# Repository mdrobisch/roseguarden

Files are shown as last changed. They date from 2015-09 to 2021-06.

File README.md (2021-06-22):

RoseGuarden
===========

A remote door api and web application for Raspberry Pi, Odroid, Orange Pi or BeagleBoard (based on python).

Important news
==============

**Because of issues in the very base of the system design, we decided to make a compelete rework of roseguarden**
**Ther will be no bugfixes or features in this version of roseguarden**

Features
========

* affordable access-control system
* authentication by rfid-tags or webserver-application (smarthone, tablet)
* easily extendable for additional doors. through network based system
* 3 different user-roles (user, supervisor, admin) for managing accesses and viewing logs
* different types of accesses (period, days-budget)
* additional options to adjust accesses (by given time, weekdays, differenet door-licences)
* basic statistics (total users, total accesses, accesses per weekday, accesses per door/node)

Roadmap
=======

Roseguarden is in development. Till now there exist only a prerelease version. It's already working fine and can be installed/ setup using the instruction below. So far it is not a released version. The following steps are planed till release and further. While there is only one contributor to the project by now, don't expect a release soon. It's done when it's done. Find news about the progress in the community-forum.

* ~~Build up and run a community forum~~ [Finished 2017-01-17 [Community forum](http://www.community.fabba.space/)].
* ~~Integrate the http-server into flask~~ [Finished 2017-02-19].
* Implement a web-gui setup to make setup easier. [In development]
* Package Roseguarden into images (ISO) for Raspberry Pi 2, 3 and Zero. [planned]
* Provide a user manual for important task and usage of Roseguarden [planned]
* __**Release version 1.0.0 images**__ [planned]
* Integrate a tool to repair broken rfid-tags [planned]
* Build a web-gui export and import feature for user-backup [planned]
* Build in user groups for easy handling of multiple users [planned]
* __**Release Version 1.1.0**__ [planned]

Backlog for further release:
---------------------------

* OLED display support
* Replace SPI-Py package with a more stable module
* Rework RFID-module
* support for machine-control (enable/license machines)
* support a cashless payment system

News & Community
================

**Want to see Roseguarden in action: Visit Roseguarden on the Maker-Faire-Saxony in Chemnitz Germany (22./23. April 2017)**

The project has a community forum. News will be posted there. In addition its purpose is to find help, discuss features or report bugs. You are welcome to contribute to the project there.

[To the community forum](http://www.community.fabba.space/)

Overview
========

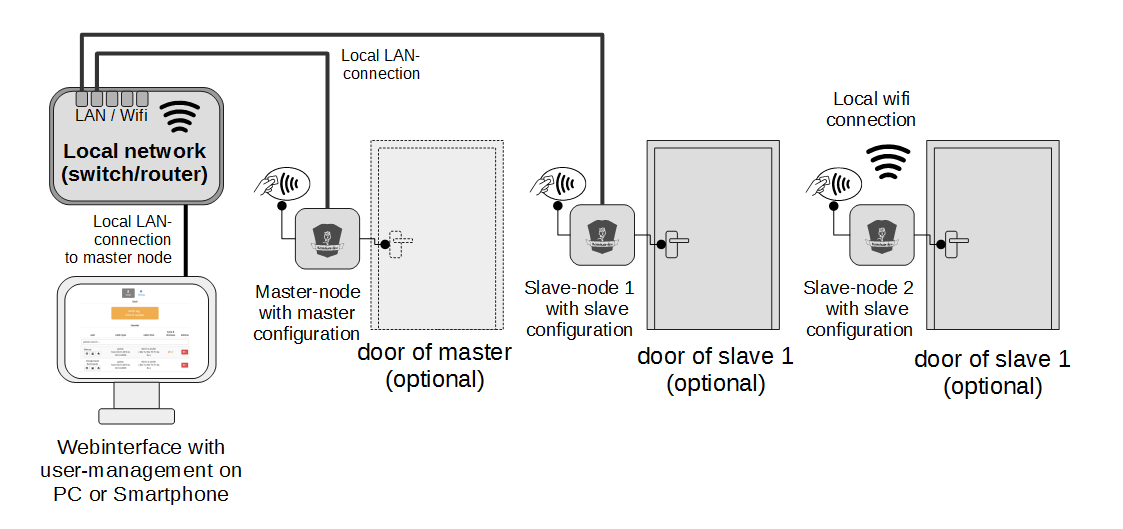
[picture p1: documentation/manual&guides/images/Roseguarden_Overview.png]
overview


Quickstart
==========

Update your system
------------------

First of all update and upgrade your raspberry pi os

1. `sudo apt-get update`
2. `sudo apt-get upgrade`

Install basic dependecies
-------------------------

3. `sudo apt-get install git`

Install RoseGuarden
-------------------

Clone the repository to your installation path with `git clone https://github.com/blinzelaffe/roseguarden.git`

Install dependencies
--------------------

For the frontend we need nodejs to get a module called bower and a fast nodejs http-server.
The http-server serve the http-request. Bower will handle all the frontend dependencies.
You can install the most actual nodejs package like this.

4. `wget http://node-arm.herokuapp.com/node_0.10.36_armhf.deb`
5. `sudo dpkg -i node_0.10.36_armhf.deb`

NOTE: for the old raspberry pi the nodejs 0.10.36 is used. Some newer versions have problems with the c++ libaries.
Have a look at http://weworkweplay.com/play/raspberry-pi-nodejs/ for further informations and instructions.
The newest nodejs-version 4.2.1 suppose to have direct raspberry pi (ARM6/ARM7) support included.
It has to be tested with RoseGuarden.

Alternative way to install LTS version of nodejs (4.2.4) for raspberry pi

for raspberry pi A,B,B+ :
wget https://nodejs.org/dist/v4.2.4/node-v4.2.4-linux-armv6l.tar.xz
tar -xvf node-v4.2.4-linux-armv6l.tar.xz
cd node-v4.2.4-linux-armv6l
sudo cp -R {bin,include,lib,share} /usr/local/

or for raspberry pi 2:
wget https://nodejs.org/dist/v4.2.4/node-v4.2.4-linux-armv7l.tar.xz
tar -xvf node-v4.2.4-linux-armv7l.tar.xz
cd node-v4.2.4-linux-armv7l
sudo cp -R {bin,include,lib,share} /usr/local/

First we install the nodejs-http-server
For this step you have to switch to the `client`-directory and prompt

6. `sudo npm install -g http-server`

Now we could install bower and let bower get us the packages for the frontend (css, angularjs, smarttable, etc.).
In the same `client`-directory prompt

7. `sudo npm install -g bower`
8. install the bower packages with `bower install` (in the `client`-directory install)

Now the frontend is ready.

For the backend (python) we have to install dependecies, too.

First we install `python-dev` and `gcc` on the raspberry to establish interfaces between c++-libs and python.

9. `sudo apt-get install python-dev` needed to compile c++-bindings with python
10. `sudo apt-get install gcc libjpeg-dev zlib1g-dev` needed to compile c++, jpge and zlib

The python package manager `pip` will handle needed python modules for us. So we need to install `pip` like this.

11. `sudo apt-get install python-pip`

At this point we will get the python packages list in the `requirement.txt` file.
Switch to the `server`-directory and prompt.

12. `sudo pip install -r requirements.txt` (in the `server`-directory)

To use the rfid-reader (rc522) we have to install SPI-Py. Switch to the `server/app/SPI-Py`-directory and
install the dependencies and the module.

13. `sudo python setup.py install` install the module

Note: depending on your raspberry pi and kernel you have to re/enable the spi-module and the device tree support
with `sudo raspi-config` -> 'Advanded Options'

Initial steps
-------------

- copy the template `config.template.ini` in the `server` - directory to `config.ini` with `cp config.template.ini config.ini`
- change settings to your requirements
- initialize RoseGuarden database in the `server` - directory with `sudo python roseGuarden.py create_db`

Running RoseGuarden
-------------------

- start the http-server in the `client` - directory with  `http-server -p 8000`
- start the RoseGuarden-app in the `server` - directory with `sudo python roseGuarden.py start`

Use RoseGuarden
----------------

- after complete installation and setup you can reach the admin panel on the ip of your raspberry pi (port 8000)
- e.g. enter "192.168.1.100:8000" in your browser (Chrome or Mozilla are suggested)

- The initial administrator-account is: Administrator
- The initial administrator-password is: pleasechangethepassword
- please change the password after your first login

Problems durring installation and running RoseGuarden
-----------------------------------------------------

** _Problem:_ **

Modules (e.g. Flask) could not found while running `sudo python roseGuarden.py create_db` or `sudo python roseGuarden.py start`

** _Solution:_ **

- Go to `/your-roseguarden-directory/server/`
- repeat the installation of the python modules with `sudo pip install -r requirements.txt`
- sometime there are problems with a bad internet connection, check this twice before running the installation (e.g. ping to a known web-site)

** _Other Hints:_ **

Some other known issues regarding the WLan and the RFID-Reader can be found at the end of the page.

Have a look at the known issues on Github ( https://github.com/blinzelaffe/roseguarden/issues?utf8=%E2%9C%93&q=is%3Aissue+ ) and see problems already known.

Sometimes a update will help to get the latest version of RoseGuarden and some fixed bugs. See the section below for this.

Update RoseGuarden
------------------

For updating RoseGuarden stop its running process.

To update the software to the latest version on github, use git.

- `git fetch --all`
- `git reset --hard origin/master`

Now switch to the `server`-directory:

If some new external pip-modules are introduces in a version you need to reload the `requirements.txt`.

- `sudo pip install -r requirements.txt`

In addition a upgrade of the migration from the database is required, use roseGuarden.py.

- `sudo python roseGuarden.py db upgrade`

For migrations or upgrades of the database, new data have to been seeded (storing default values). So please run,

- `sudo python roseGuarden.py seed`

To update the client switch to your client directory e.g the `client`-directory:

Here we have to install/uninstall all new/old packages of bower.

- `bower install` (no `sudo` required)

After updating please restart your roseGuarden-application again.
It should be work after this with the newest version for server and client.

Install autostart and montoring (supervisor)
============================================

After testing roseGuarden on the system you can add a autostart and monitoring of the application and the http-server.
We use supervisor for this purpose.

You can install supersior from distribution package

- `sudo apt-get install supervisor`

- `sudo service supervisor restart`

The config of supervisord is stored on your system in the following file: `/etc/supervisor/supervisord.conf`.
There is a template in the repository `documentation/templates&scripts/supervisord.config`.
Use the file to adapt it to your system (especially the pathes).

Screenshots (Software)
======================

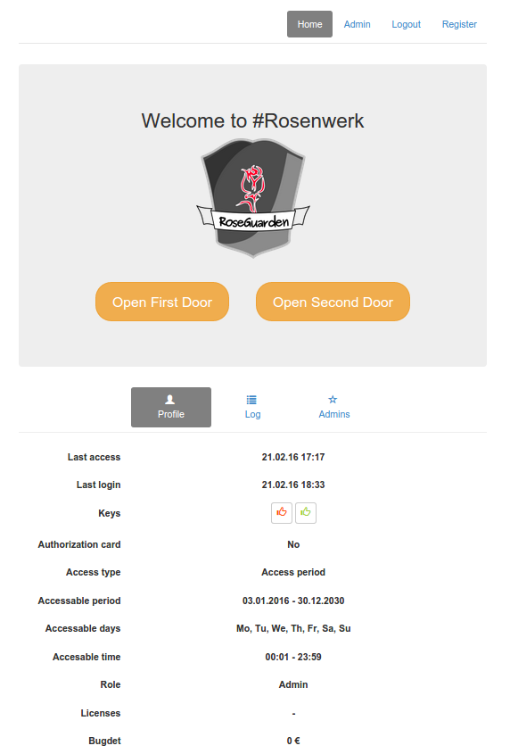
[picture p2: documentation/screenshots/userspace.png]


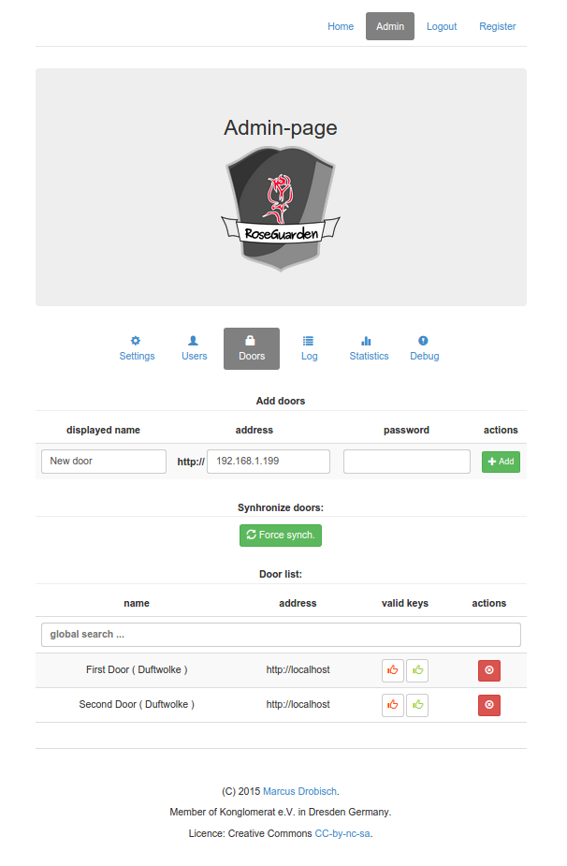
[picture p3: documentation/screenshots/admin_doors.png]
doors


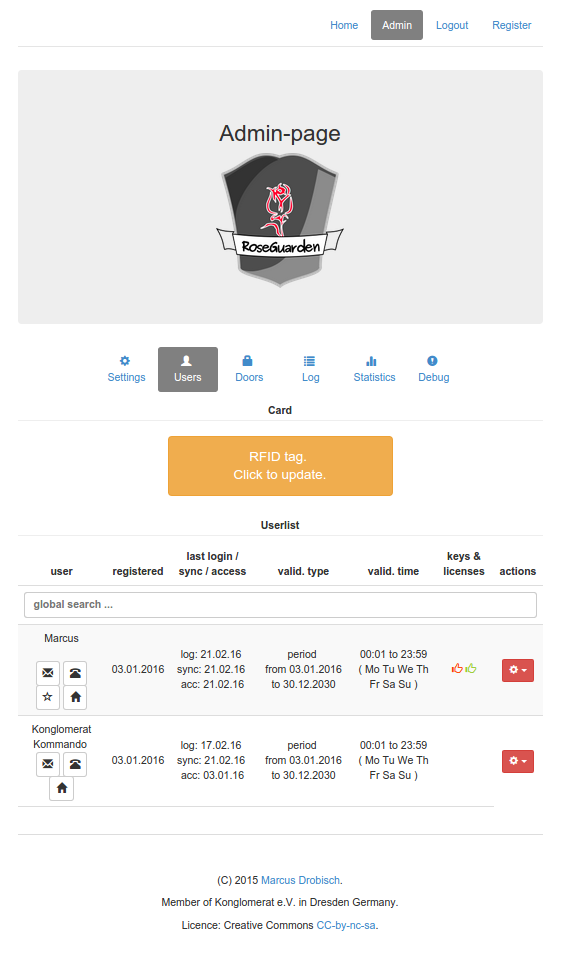
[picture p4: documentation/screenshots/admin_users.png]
users


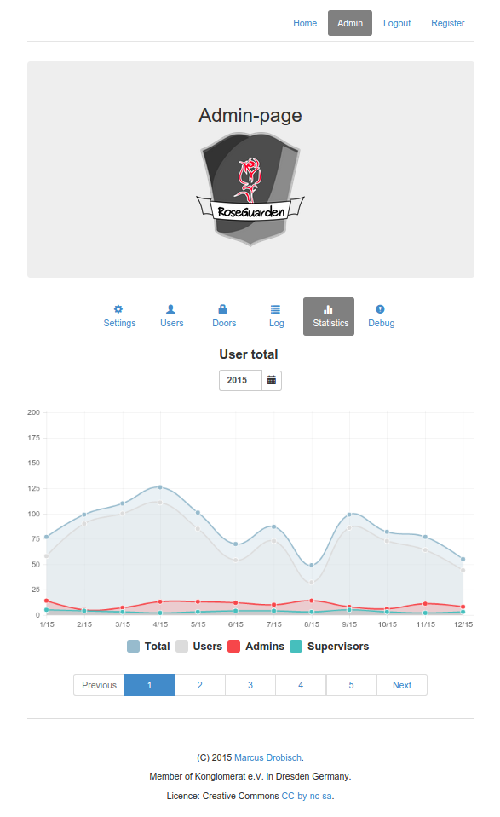
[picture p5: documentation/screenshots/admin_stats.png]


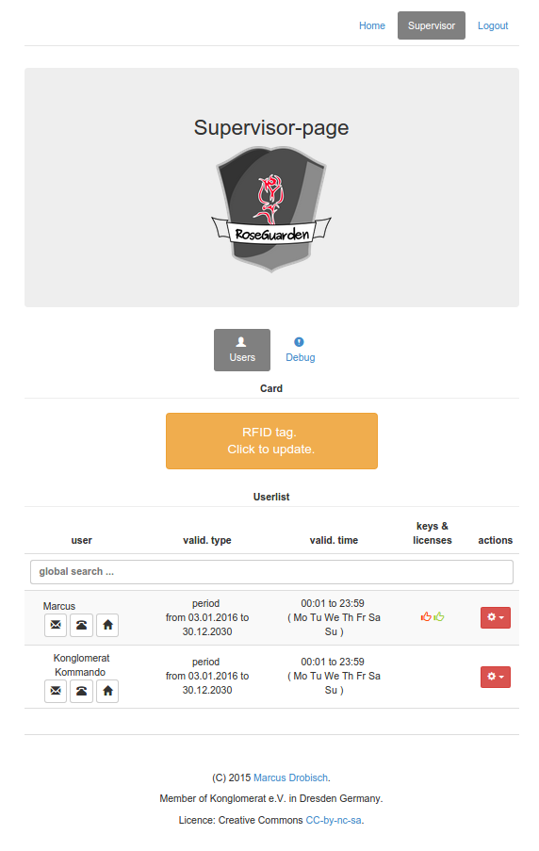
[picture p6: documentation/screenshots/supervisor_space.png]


Hardware
========

The hardware consists of the following electronics  types mounted on a board.

- the control unit (Rapsberry Pi, Orange Pi, Beagleboard or Odroid): running the Python based app and server.
- a RFID-reader (e.g. RC552): reading and writing the tags
- a relay-module: controling the door-openers
- a dc-dc-converter: supplying the control unit with a input  of e.g. 12V / 24V and a output of 5V
- a micro-usb cable of 30cm length: connect dc-dc-converter to the control unit
- some internal cable: e.g. from dc-dc converter to the relay module or to the raspberry pi

Screenshots (Hardware)
----------------------

Here some photos of the assembled and mounted Roseguarden device in the early stage.

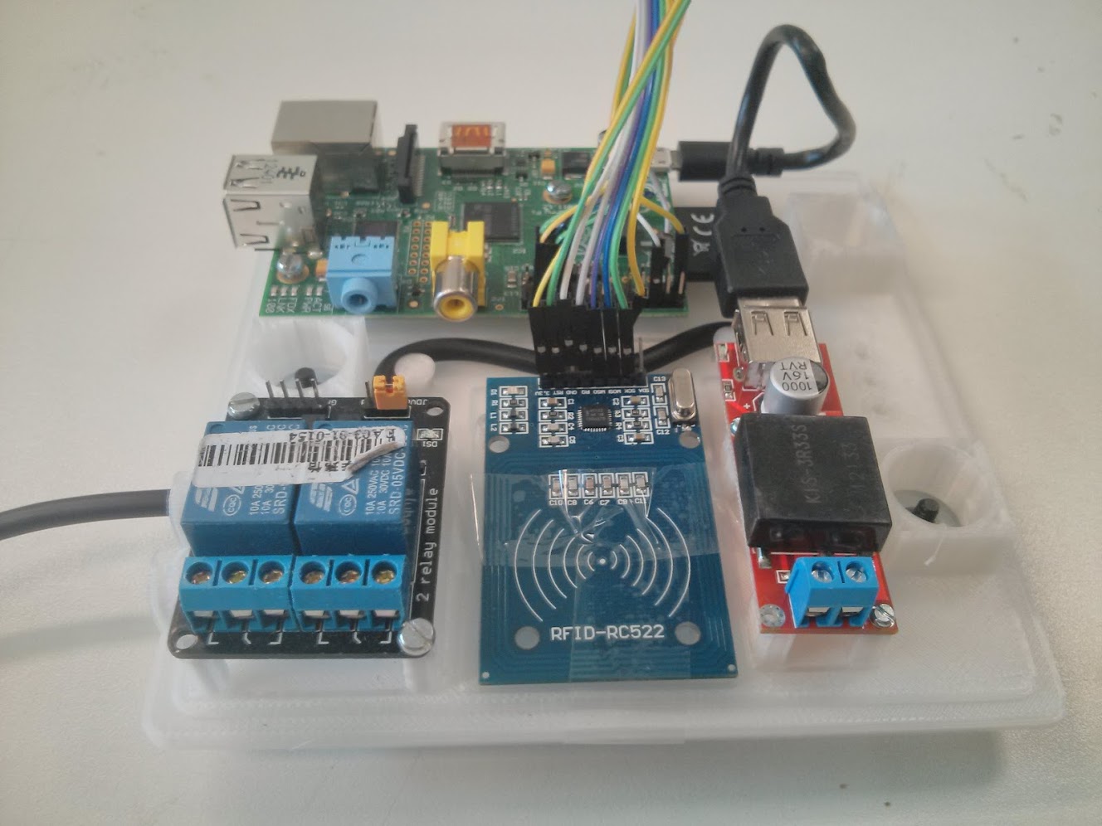
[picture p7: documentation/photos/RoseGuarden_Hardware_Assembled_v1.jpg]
 

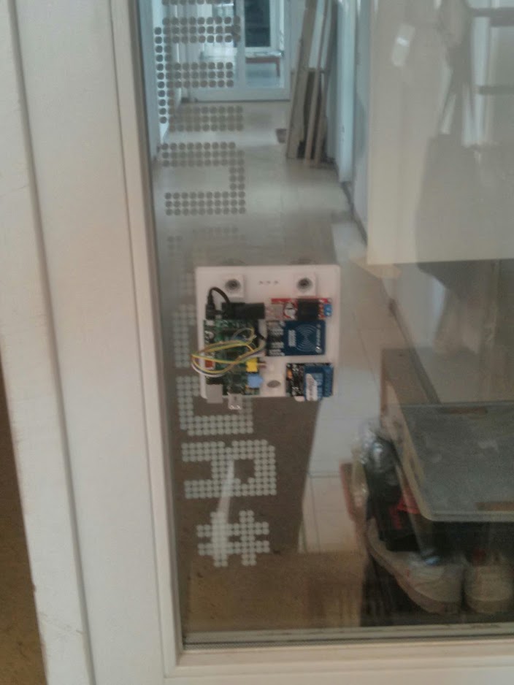
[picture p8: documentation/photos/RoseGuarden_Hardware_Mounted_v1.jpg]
 

Recommended bill of material
----------------------------

We recommend the following tested devices:

- Rapsberry Pi 1 B (found on watterot, rs online, digikey)
- KIS3R33S dc-dc converter (found on ebay from various distributoirs from about 3€ per piece)
- RC552 rfid reader, including 2 rfid-tags (found on ebay from various distributors from about 3€ per piece)
- SainSmart 2 ch. relay module or compatible (found on ebay from various distributors and producers from about 3€ per piece)
- the 3d-printed case on below
- 4 x M2 and 10 x M3 screws to mount the electronic to the case

additional for connecting and supllying the device:

- some breadboard female-female connector (found on pollin, watterot or sparkun)
- some cable with at least 3 wires @ 1A (found on pollin, reichelt, digikey or your local electronic store)
- a ethernet-patch-cable (found on pollin, reichelt, digikey or your laocal electronic store)
- or a wifi-dongle (found on pollin, reichelt, digikey or your laocal electronic store)

additional for mounting the device on walls or doors:

- suckers with 40mm diameter and M4-bolts (found on ebay from various distributors from about 7€ per 10 pieces)
- or glue tape for mounting
- or screws for mounting 

Case and Mounting
-----------------

The case ist modeled with the powerful open source software FreeCAD. Have a look in the hardware folder for the current stable version of the board and its case. It is designed to be 3d-printed with dimensions of 145mm x 145mm x 60mm. The design uses suckers to mount the device to windows or doors. With a few modifications you can also use screws for a more stable mounting. Be aware that the RFID-communication could only reach throw about 30mm non-metallic walls or glass (+ aboout 20mm rfid-module-to-wall distance). 

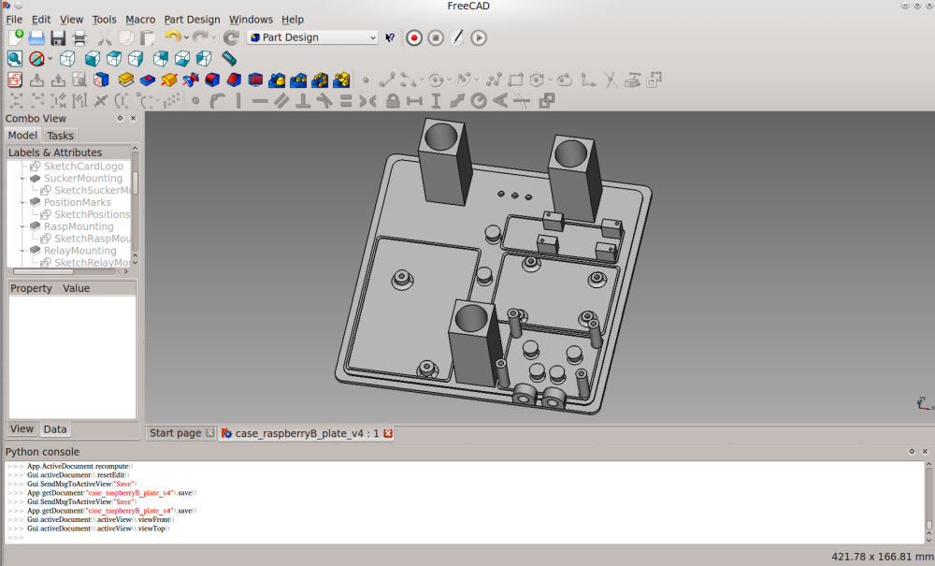
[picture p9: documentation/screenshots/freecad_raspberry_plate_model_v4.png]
freecad
 

Feel free to change the design to your needs. Please share your changed designs and new versions with the community (by asking for a push request). 

Assembly
--------

To assemble the components, you only need some additional M2 and M3 screws to put the electronics on the board. While using other electronics than recommended, change the board modell to your needs. The positions are marked for easy assembly. The cable can put throw cable holes and routed along dedicated bolts.

The schematic show the connection between raspberry pi and the modules.

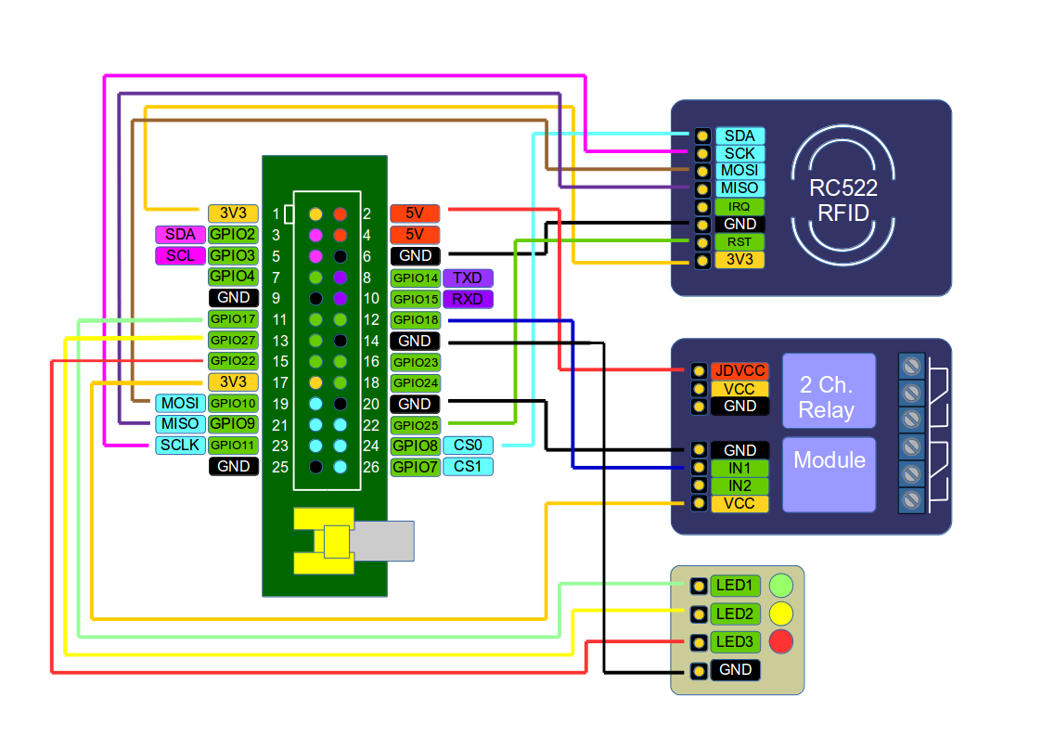
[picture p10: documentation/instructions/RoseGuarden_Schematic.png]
schematic


Further Documentation
=====================

Further documentation and information on components and installation could be found on the project-wiki http://h2371910.stratoserver.net/projects/tuer-und-geraeteverwaltung-rosenguarden/wiki/Wiki (german language only, please translate via google translate or other services).

Troubleshooting
===============

*The WLAN connection breaks ofter some time*

Normally the wlan connection timed out after a while.
The default config of raspberry pi (wheezy) don't reconnect to disappearing networks.
To fix this the following steps could enable the reconnection.

- change to /etc/ifplugd/action.d/ with `cd /etc/ifplugd/action.d/`
- copy the ifupdown file to ifupdown.original (for backup) with: `sudo cp ifupdown ifupdown.original`
- overwrite ifupdown with the alternative ifupdown from the wpa_supplicant-folder with:  `sudo cp /etc/wpa_supplicant/ifupdown.sh ./ifupdown`
- reboot with `sudo reboot`

Alternativly you can tools like wicd-curses.
Instructions for wicd-curses can be found in the internet.

*I have problems to develop under windows*

- Install the python Visual C++-Compiler from  http://aka.ms/vcpython27 before installing the requirements
- user requirements_win_dev.txt instead of requirements.txt (SPI-Py is for linux only)

*The rfid don't read any tag*

With Kernel 3.18 and above Rasbian switch to device tree support on default.
A detailed description is shown here: https://www.raspberrypi.org/forums/viewtopic.php?t=97314
This could encounter problems with the spi.

To fix the issue you have to re/enable the spi-module.
To setup this use `sudo raspi-config` -> 'Advanded Options' or write the changes directly to `/boot/config.txt`
on your own.

For Raspbbery Pi B

`dtparam=spi=on`

`dtoverlay=spi-bcm2708`

have to been set.

For Raspberry Pi 2 (not tested, yet)

`dtparam=spi=on`

`dtoverlay=spi-bcm2835`

should be working (not tested yet)

For Raspberry Pi 2 please consider, there is be a another pin-out-connectio needed. Some instructions described here:
https://www.raspberrypi.org/forums/viewtopic.php?f=37&t=106313 or a alternative way to enable SPI here http://bsd.ee/~hadara/blog/?p=1017

Mifare_RC522_RFID Raspberry Pi 2 B

MOSI ——————————> pin 19 e.g. GPIO 10

MISO ——————————> pin 21 e.g. GPIO 9

SCLK ——————————> pin 23 e.g. GPIO 11

SDA  ——————————> pin 24 e.g. GPIO 8

RST  ——————————> pin 22 e.g. GPIO 25

IRQ  ——————————> NONE

In addition you have to change your SPI-Py library. There is a bug, which isn't fixed and break the communication to the Mifare-Module.

change the following code in the `/server/app/SPI-Py/spi.c`-file.

```c
	struct spi_ioc_transfer tr = {
		.tx_buf = (unsigned long)tx,
		.rx_buf = (unsigned long)rx,
		.len = tupleSize,
		.delay_usecs = delay,
		.speed_hz = speed,
		.bits_per_word = bits,
        .cs_change = 1,
    };
```

to

```c
	struct spi_ioc_transfer tr = {
		.tx_buf = (unsigned long)tx,
		.rx_buf = (unsigned long)rx,
		.len = tupleSize,
		.delay_usecs = delay,
		.speed_hz = speed,
		.bits_per_word = bits,
        .cs_change = 0,
	};
```

License
=======

RoseGuarden is published under the terms of the GPL v3 license. See [LICENSE](LICENSE).

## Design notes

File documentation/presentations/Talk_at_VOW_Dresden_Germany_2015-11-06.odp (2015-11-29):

## DIE FLEXIBLE WERKSTATT ZUTRITTS-, BUCHUNGS- UND BEZAHLSYSTEME 5.11.2015 Dresden

## Herzlich Willkommen

Willkommen

- Voträge & Workshop
- 10 – 12 Uhr: Vorträge
- Anschließend Mittagspause
- 14 – 16 Uhr: Workshop
- ~~Achtung Webcam~~
- Unterlagen unter:https://github.com/blinzelaffe/roseguarden & http://h2371910.stratoserver.net/

## Zur Person

Willkommen

- Marcus Drobisch
- Mitglied im Konglomerat e.V.
- Untergruppe FabLabDD
- Interesse an: Menschen, Elektronik, Open Source, Zeichnen
- Baustellen: Elektronikecke & Zutrittskontrolle
- Ausbildung: Dipl. Elektrotech. Vertiefung Feinwerktechnik

## Und ihr ?

## Agenda

Willkommen

- Thema & Problemstellung
- Rechtliches & Versicherung
- Bestehende Lösungen
- Gastvorstellungen
- Vorstellung RoseGuarden
- Möglichkeiten der Zusammenarbeit

## Literatur & Links

Thema

- Wenig offene Informationen
- Sehr zerstückelte Teilinfo. (google.de etc.)
- Grobe Informationen bei:
  - Abus
  - Sicher24.de
  - Dormas
- Anlaufpunkt unser Wiki

## Literatur

Thema

- Praxis-Ratgeber Zurittssteuerung vom Bundesverband für Sicherheitstechnik e.V
- Gute Übersicht
- Viel Werbung
- Trotzdem guter Einstieg
- 14,95€ direkt bei BHE

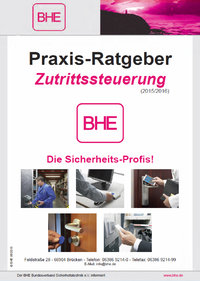
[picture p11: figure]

Quelle: http://www.bhe.de/

## Thema & Problemstellung

Thema

- Sehr Facettenreiches Thema
- Betrifft fast jede größere Gruppe
- Finanzielle und Arbeitstechnische Belastung
  - Komerzielle Systeme sehr teuer und „closed“
  - Unklarheiten zur Anforderung
  - Unsicherheiten bei Recht. und Versicherung
  - Keine neutrale Anlaufstelle
  → daher viele Eigenentwicklungen

## Um was geht es heute

Thema

- Grober Überblick zu den wichtigsten Aspekten
- Anlaufpunkt für Hilfesuchende
- Interesse wecken und entmystifizieren
- Vorstellung von Lösungen
- Möglichekeiten der Zusammenarbeit ausloten
- Spass haben

## Um was geht es nicht

Thema

- Detailierte Betrachtungen ist nicht möglich
- Konkrete/vollständige Einzellösungen
- Zusatzfunktionen wie Buchungssystem oder Bezahlsystem (werden nur angeschnitten) → Workshop
- Rechtliche „Beratung“ nicht möglich
- Technische „Beratung“ ebenfalls nicht

## Vorteile Zutrittssteuerung

Thema

- Zutritts nach „Wer, Wann, Wo, Wie“ möglich
  - z.B. Teilzutritt, Zeitl. Begrenzung, Gast-Accounts
- Schlüssel sind günstig / kostenlos
- Schlüsselverlust ist kein Problem (Verwaltung)
- Statistische Auswertung des Besucherflusses
- Sicherheitsaspekte (Erkennung von Einbrüchen)

## Vorteile Zutrittssteuerung

Thema

- Zusatzfunktionalität
  - Benutzerausweis
  - Berechtigungssysteme (auch für Geräte)
  - Bezahltsysteme möglich
  - Mitgliederverwaltung
  - Buchungssysteme
  - Kopplung an ERP-Systeme / Datenbank / Systeme
  - Weitere Ideen ?

## Nachteile Zutrittssteuerung

Thema

- Weiterhin Angreifbar (Hacker müssen Hacken)
- Manipulation nicht immer sichtbar
- Akzeptanz der Nutzer
- Ausfallsrisiko
- Personen- und Datenschutz
- Rechtliche uns Versich.-technische Belange

## Rechtliches

Recht&Ver.

- Personenschutz
- Mietrecht
- Datenschutz
- Normen & Richtllinien

## Rechtliches: Personenschutz

Recht&Ver.

- Das System muss elektr. sicher sein
  - Achtung bei Netzspannung (Elektrofachkraft)
  - Achtung bei Klemmgefahr
- Niemanden Einsperren / Aussperren
- Baurechtliches Vorschriften
  - Fluchtwege müssen offen bleiben
  - Brandschutz darf nicht beeinträchtigt werden
- Unfallverhütungsvorschriften

## Rechtliches: Mietrecht

Recht&Ver.

- Einbau eines Systems ist mit dem Vermieter abzustimmen
- Er darf dies nicht verwehren (AG Schöneberg, 7 C 249/89) aber Rückbau bei Auszug fordern
- Er hat kein Interesse an:
  - Verletzung seiner rechtlichen & versicher. Aspekte (Baurecht, Versicherbarkeit, etc.)
  - Einbruch & Zutritt von zu vielen Unbekannten
  - Kosten

## Rechtliches: Mietrecht

Recht&Ver.

- Je nach Umfang der Änderungen, den Vermieter schnell über Vorhaben informieren
- Zusammen Lösungen disk. und auswählen
- Andere Mieter mit ins Boot holen
- Kosten können ggf. geteilt werden
- Bei großen Objektverwaltern schwierig
- Dieser Prozess braucht Zeit

## Rechtliches: Datenschutz

Recht&Ver.

- Es gilt das Bundesdatenschutzgesetz
- Zu schützen sind z.B.:
  - Name & Anschrift, Geburtsdatum, Bankverbind.
  - Aber Daten die zu Personenprofile genutzt werden können sollten geschützt werden
- Verantwortlich ist der Vorstand
- Bis zu 50000€ Strafe / Abmahnkosten
- Man muss trotzdem keine Angst haben

## Datenschutz für Vereine

Recht&Ver.

- Empfehlung:
  - Datenschutzerklärung zum Beitrittsformular
  - Regelung zum Datenschutz in der Satzung
  - Datenschutzbeautragte ernennen
  - Diskussion des Thema
  - Ggf. rechtliche Beratung einholen (Jurist, Verbände)
- http://www.iww.de/vb/archiv/bundesdatenschutzgesetz-gilt-auch-fuer-vereine-datenschutz-im-verein-diese-massnahmen-muss-der-vorstand-ergreifen-f18138

## Normen & Richtlinien

Recht&Ver.

- Bei Eigenbauten sollte sich an Normen & Richtlinien gehalten werden
- Ggf. Versicherungstechnisch relevant
- Normen:
  - DIN EN 50133-1/ 2 / 7 „Zutrittskontroolanlagen für Sicherungsanwendungen“
  - DIN EN 60839-11-4 „ Elektronische Zutrittskontrollsysteme“

## Versicherungstechn. Aspekte

Recht&Ver.

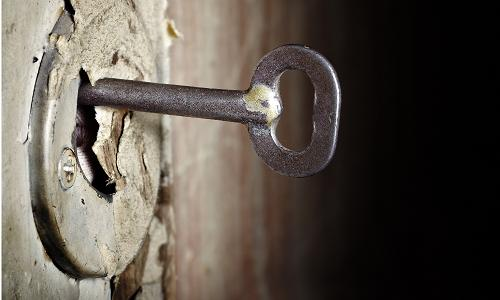
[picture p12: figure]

## Versicherungstechn. Aspekte

Recht&Ver.

- Welche Versicherung?
  - Einbruchsversicherung (z.B. des Vermieters)
  - Geräteversicherungen
  - Haftplficht
- Entweder Police sehr hoch oder Leistung niedrig (evt. sehr schlechte Zahlungsmoral)
- Verbund offener Werkstätten hilft weiter

## Versicherungstechn. Aspekte

Recht&Ver.

- Ein allgemeines Beispiel:

Die Tatsache allein, dass das Spurenbild innerhalb eines Hauses auf einen stattgefundenen Diebstahl hindeutet (durchwühlte Schränke und Behältnisse, beschädigte Möbelstücke u. ä.), muss nicht mit hinreichender Wahrscheinlichkeit den Rückschluss auf einen Einbruch zulassen. Zweifel sind insbesondere dann angebracht, wenn keine Spuren an Fenstern auf einen Einbruch hindeuten.

(OLG Köln, 9 U 32/97)

## Versicherungstechn. Aspekte

Recht&Ver.

- Ein technisches Beispiel:

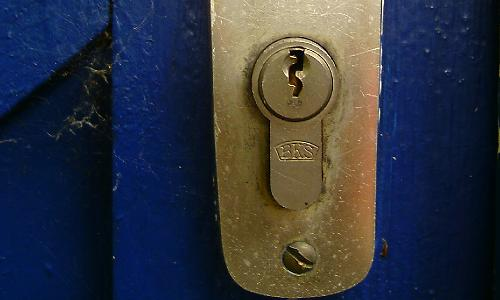
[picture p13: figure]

## Versicherungstechn. Aspekte

Recht&Ver.

- Von Außen nicht abschraubar
- Türzylinder steht nur wenig über
  - Alternativ (mit Schutzrossette)
  - Oder geteilter Zylinder
- Außen Knauf / Innen Klinke
- Verrriegelung interessant
- Sicherheitsklassen 0 - 4
  Besser:

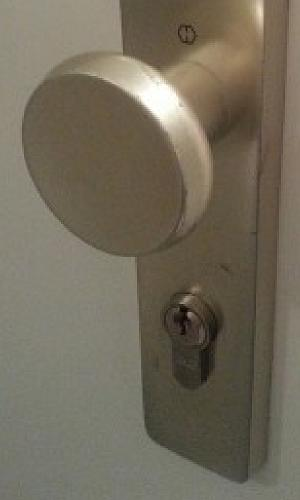
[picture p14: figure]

## Versicherungstechn. Aspekte

Recht&Ver.

- Versicherungen leider sehr intransparent
- Sprecht mit eurer Versicherung
  - Relevanz abklopfen
  - Bilder zeigen
  - Optionen vorschlagen
- Meist ist nur die Tür / das Schloss interessant
- http://ruch-finanzberatung.de/hausratversicherer -uneinig-bei-tuerschloessern/

## Bestehende Lösungen

Lösungen

- Viele Lösungen am Markt → unübersichtlich
- Unterschiedliche Ansatzpunkte
  - Komplettlösungen
  - Modulsysteme
- Unterscheiden sich im Ansatz
  - Authentifizierung
  - Türen/Schlösser
  - Verwaltung

## Lösungen - Authentifizierung

Lösungen

Wenig Mögl.

- Zahlencodes,
- Fingerabdruck
- RFID / NFC,
- Dongles,
- Webserver

Einfach

Komplex

Viele Mögl.

## Lösungen - Authentifizierung

  Quelle: www.dorma.com

Lösungen

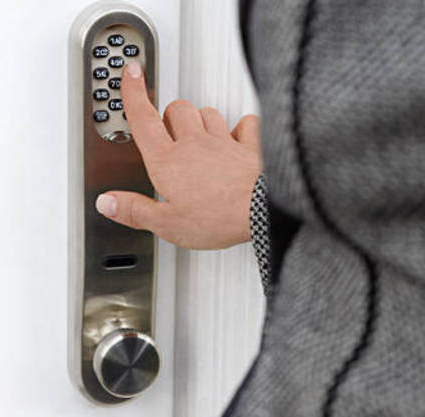
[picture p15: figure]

- Zahlencodes

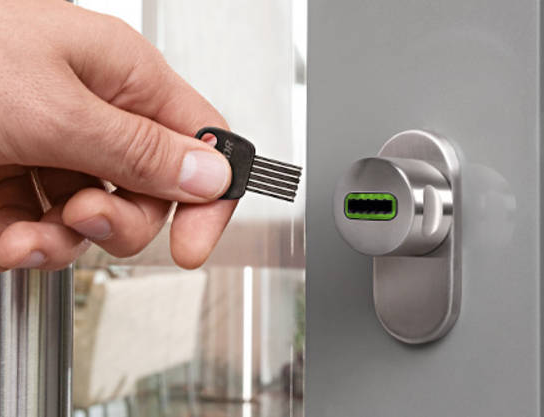
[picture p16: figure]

- Dongles

## Lösungen - Schlösser

Lösungen

Wenig Mögl.

Einfach

- Voll Integriert,
- Türlösungen
- Modular

Komplex

Viele Mögl.

## Lösungen - Schlösser

  Quelle: www.dorma.com
  Quelle: www.dorma.com

Lösungen

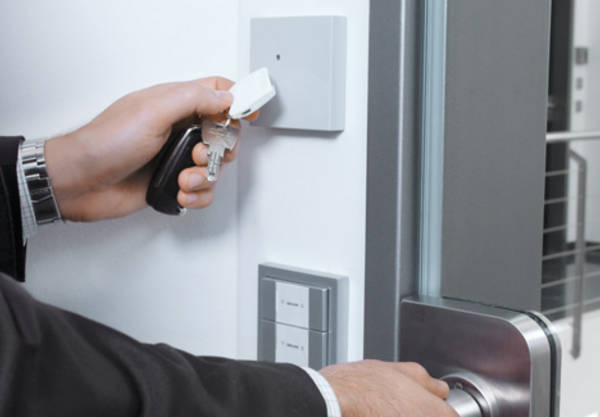
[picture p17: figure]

- Türlösungen

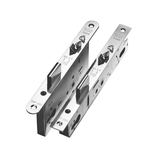
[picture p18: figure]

- Modular

## Lösungen - Verwaltung

Lösungen

Wenig Mögl.

Einfach

- Integriert
- Datenbank
- Webserver

Komplex

Viele Mögl.

## Lösungen - Verwaltung

  Quelle: www.dorma.com
  Quelle: www.nuki.io

Lösungen

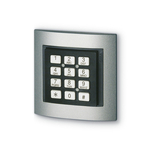
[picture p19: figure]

- Integriert

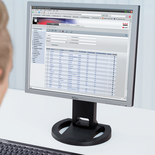
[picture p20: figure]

- Datenbank

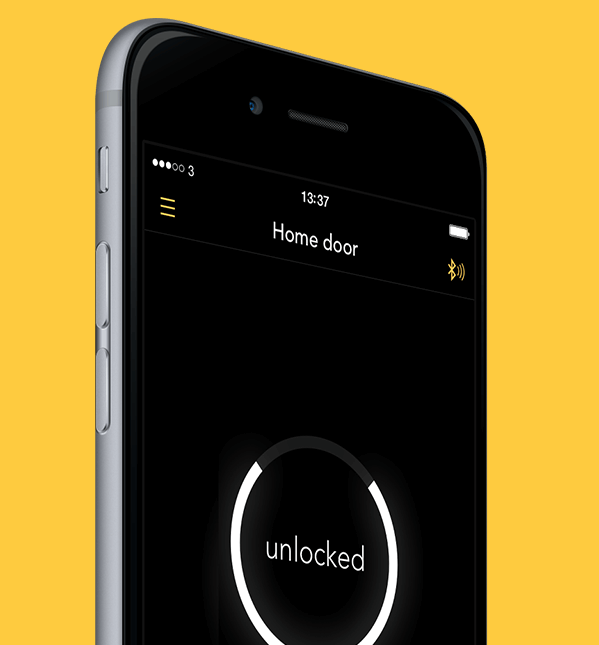
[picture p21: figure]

- Webserver

## Vorteile komerz. Lösungen

Lösungen

- Kein Know How benötigt (Fachmänner)
- Installation je nach Anbieter sehr schnell
- Meist keine Kinderkrankheiten mehr
- Garantie im Falle eines Ausfalls
- Große Namen (wie Abus) kommen bei Versicherungen gut an
- In einigen Fällen guter Support (Handbücher, Schulungen, Hotlines)

## Komerzielle Angebote

  Quelle: www.nuki.io

Lösungen

- Nuki

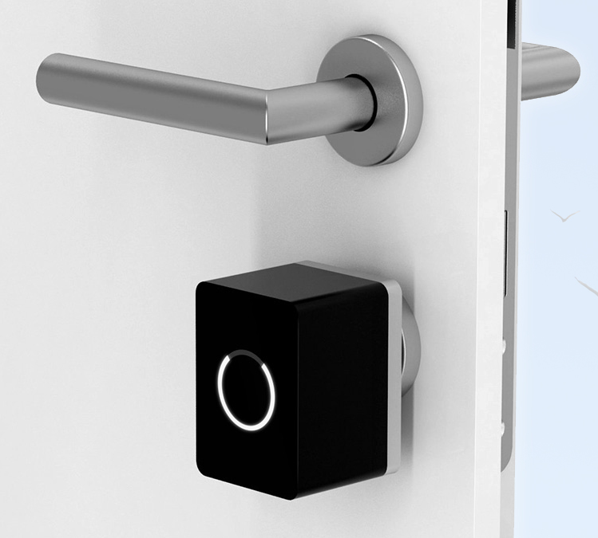
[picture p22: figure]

## Komerzielle Angebote

  Quelle: www.dorma.com

Lösungen

- Dorma

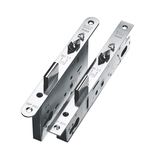
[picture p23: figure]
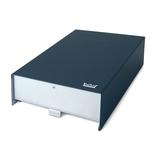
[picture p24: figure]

## Komerzielle Angebote

  Quelle: www.delta.de

Lösungen

- Net2 Türsteuerzentrale (DELTA)

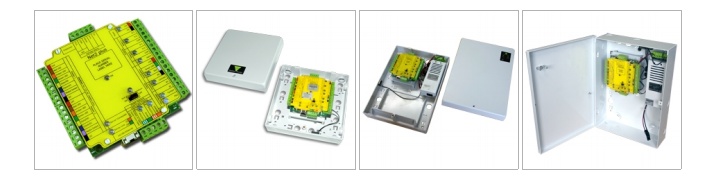
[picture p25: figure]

## Komerzielle Angebote

  Quelle: www.abus.de

Lösungen

- Abus

## Nachteile komerz. Lösungen

Lösungen

- Kosten:
  - Net2: ca. 1000€ + 300€ pro Tür + Trans.
  - Dorma/Abus: ca. 1K5 € + 300-800€ pro Tür + Trans.
  - Service- und Installationskosten
- Nicht erweiterbar (Buchungssystem, ERP, Bezahlsystem)
- Service / Know How liegt extern
- Spaß am eigenen Projekt fehlt

## Pause :-)

## Open Source Lösungen

Freie Lös.

- Hier können nur Open Source bzw. öffentl. dokumentierte Lösungen vorgestellt werden
- Bei Interesse oder Details die Fabs oder Spaces einfach direkt anfragen.

## UACS – Erlangen

Freie Lös.

- Universal access control system
- FAU Lab Erlangen (Koop. mit der Universität)
- Technik:
  - Eigene Hardware Arduino Basis (C)
  - Touchscreen Display
  - RFID-Karten (Mifare Classics wie FabLabDD)
- Link: https://github.com/fau-fablab/uacs-hardware
- Kosten/Aufwand: unkenannt, sehr individuell

## Spaceportal – Bamberg

Freie Lös.

- Backspace Bamberg
- Technik:
  - Basiert auf ABUS HomeTec CFA 1000
  - Webinterface in Python (py-dooropener)
  - Backend in Flask (wie in FabLab DD)
- Link: https://www.hackerspace-bamberg.de/Spaceportal
- Kosten/Aufwand: unkenannt, sehr individuell

## BenutzerDB – Mannheim

Freie Lös.

- Backspace Bamberg
- Technik:
  - PinPad
  - Hometec Controller
- Link: https://github.com/raumzeitlabor/rzl-benutzerdb https://wiki.raumzeitlabor.de/wiki/Pinpad
- Kosten/Aufwand: unkenannt, sehr individuell

## Weitere Lösungen

Freie Lös.

- Gute Lösungen von Labs und Spaces ohne öffentliche Dokumentation
  - FabLab Bremen e.V.
  - FabLab Berlin (Makea Industries GmbH)
- Auch hier bei Interesse einfach anfragen

## Jemand vergessen? Bitte schreibt mir m.drobisch(at)googlemail.com

Freie Lös.

## Internationale Lösungen (eng.)

Freie Lös.

- Gut dokumentierte internationale Lösungen
  - DoorAcces von TkkrLab https://www.tkkrlab.nl/wiki/DoorAccess
  - MakerAccessControl von roycepipkins https://github.com/roycepipkins/MakerAccessControl
  - RFID Door Lock Shield von freetronics http://www.freetronics.com.au/products/dlock-rfid-door-lock-shield
  - Arduino RFID Door Lock von pcmofo http://www.instructables.com/id/Arduino-RFID-Door-Lock/

## Internationale Lösungen (eng.)

Freie Lös.

- Weitere internationale Lösungen
  - LinuxMCE http://www.linuxmce.org/
  - USB Auth von Makerslocal https://256.makerslocal.org/wiki/index.php/USB_Auth
  - GSM Access Control System von Elab Hackspace http://www.thebitbangtheory.com/2013/11/elab-hackerspace-gsm-access-control-system/
- Oder einfach nochmal mit google oder duckduckgo selbst auf die Suche gehen

## Einschub Kassensystem

Freie Lös.

- Sehr detailiertes Kassensystem-Projekt des FAU Lab Erlangen
  - Weitestgehend Open Source
  - Holzkasten, Scheinaufnahme Münzsammler, PC und Touch
  - Software in Python
  - Anschluss an ERP (Odoo)
  - https://user.fablab.fau.de/~buildserver/presentations/kassenterminal.pdf
  - https://github.com/fau-fablab/FabLabKasse

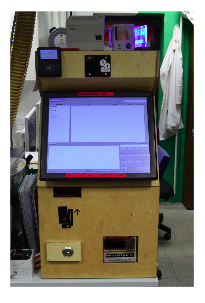
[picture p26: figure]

## Fazit: Freie Lösungen

Freie Lös.

- Sehr viele sehr spannende Lösungen vorh.
- Jedoch viel Detailwissen zur Umsetzung oder Adaptierung notwending
  - Sehr individ. angepasst auf eigene Spaces/Labs
  - Meist sppezielle Baugruppen verwendet
  - Oft keine Standard-Werkzeuge und -Software
  Schwieriger Einstieg für Anfänger oder technisch wenig Interessierte

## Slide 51

RoseGuarden

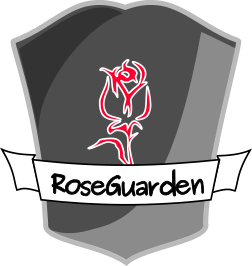
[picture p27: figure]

## RoseGuarden - Allgemeines

RoseGuarden

- Lösung des FabLabDD / Konglomerat e.V.
  - Hervorgegeangen aus Zutritts/Schlüsselproblem und Eigenbau-Laser-Projekt
- Zielsetzung:
  - Gute Dokumentation (anfängerfreundlich)
  - Geringe Kosten (breites Einsatzfeld, niedrige Hemmschwelle)
  - Modular (erweiterbar)
  - Sicher und Zuverlässig
  - Aufbau- und Reparierbar (Standardwerkzeuge)
  - Open Source (Software und Tools)

## RoseGuarden - Übersicht

RoseGuarden

- Bisher leider nur 1 Entwickler
- Forum und Hardware-Wiki (deutsch):
  - Hilfe, Übersicht, Türen, Schlösser, Technikhttp://h2371910.stratoserver.net/projects/tuer-und-geraeteverwaltung-rosenguarden/
- Software-Übersicht mit Anleitung (englisch):
  - Git: Python, JavaScript, CSS und HTML https://github.com/blinzelaffe/roseguarden

## RoseGuarden - Software

RoseGuarden

- Webserver (Backend):
  - Python mit Flask-Framework und Datenbank
  - REST-Api mit Restful
- Benutzerseite (Frontend):
  - Javascript mit AngularJS, CSS, HTML
- Hintergrund (Background-Worker):
  - Mail-Verwaltung
  - MFRC522 Reader

## RoseGuarden - Hardware

RoseGuarden

- Platinen PC z.B. Raspberry Pi, Orange Pi, Odroid
- DC-DC Spannungswandler z.B. KIS3R33S
- Relais-Board z.B. SanSmart Relay Module
- RFID-Lesegerät z.B. MFRC522
- RFID-Karten/Tags z.B. S50 oder S70
- Türöffner z.B. von Dorcas
- Zubehör: WLAN-Stick, USB-Kabel, 12V-Netzteil, Steuerleitung, Gehäuse, Schrauben, etc.

## RoseGuarden - Kosten

RoseGuarden

- Minimalkosten Aufbau
  - Bestellungen bei AliExpress oder eBay, Versandkostenfrei, kein Zoll
  - Orange Pi: 15€, DC-DC-Spannungswanlder KIS3R33S: 2€
  - RFID-Leser MFRC522 mit 1 Karte: 2€, Relais Modul: 2€
  - Dorcas Türöffner: 18€, USB-Kabel und Kleinteile: 6€
- Zusätzliche Teile aus der Krabbelkiste/Schrott:
  - 12V Netzteil (PC, Laptop), Ethernet-Kabel oder WLAN-Stick, Kabel: 4 adrige Steuerleitung, Spannunsgversorgung
- 3D-Druck oder Laser für Gehäuse:
  - 10 Stunden 3D-Druck (bei FDM, 2 Teile)
  - Oder Lasercutter ca. 10 Minuten
- Gesamtkosten: ca. 45-85€ + Gehäusekosten

## RoseGuarden - Authentifizierung

RoseGuarden

- Web-Anwendung (Log-In)
  - Smartphone oder PC
  - Keine Apps ntowendig aber möglich
  - Vorhandeness WLAN nutzbar
  - Schnittstelle für Erweiterung (REST-API)
- Alternativ per RFID Karten

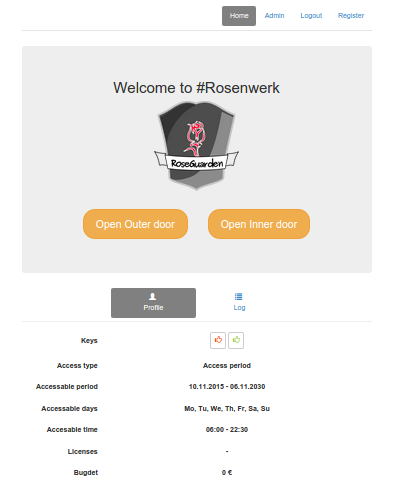
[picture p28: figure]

## RoseGuarden - Verwaltung

RoseGuarden

- Per Web-Anwendung
  - Freie Benutzeranmeld.
  - Admin-Bereich mit Freischaltung
  - Protokoll
- Zugangskontrolle
  - Räume/Türen
  - Wochentage
  - Zeitraum und Tageszeit

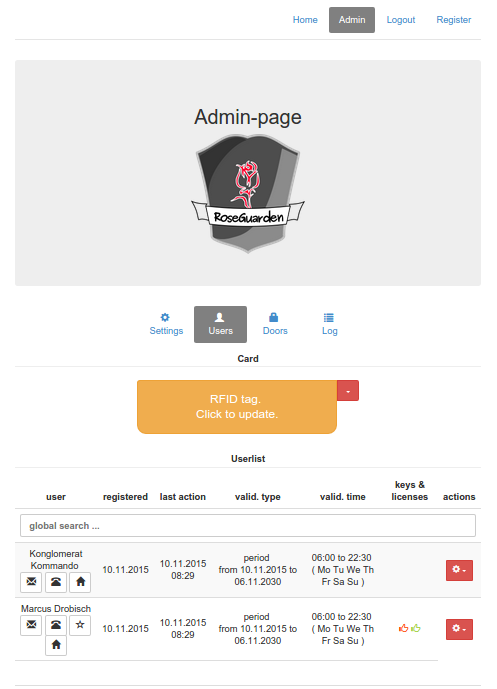
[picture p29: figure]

## RoseGuarden - Sicherheit

RoseGuarden

- Ende zu Ende Verschlüsselung möglich
  - SSL (wie Banken, Internet-Shops)
  - Zusätzlich verschlüsseltes WLAN möglich
- RFID-Tags
  - Verschlüsselte Daten auf der Karte
  - Nur geheimer Zutrittscode gespeichert, keine persönl. Daten
- TODO: Verschlüsseltung auf Einplatinen-PC, Captchas, Detektoren, Verplombung, ggf. Kill-Switch

## RoseGuarden – TODO

RoseGuarden

- Aktueller Stand: 90% der Grundfunktion fertig
- Weitere Pläne:
  - Sicherheit erhöhen (siehe Folie: Sicherheit)
  - Weitere Schlossarten (bisher nur Türöffner)
  - Benutzerbezogene Gerätefreischaltung
  - Bargeldloses Bezahlsystem per RFID
  - System zur Geräte-Buchung / Verwaltung
  - Verknüpfung mit Mitgliederverwaltung

## Zusammenarbeit

Zusammen

- Sehr viele Eigenentwicklungen
- Kopetenzen meist gebündelt
- Weiterführung bei Umzug (u.a.) gefährdet
- Zusammenlegen von Projekten
- Zusammenarbeit macht mehr Spaß
- Hilfe für Einsteiger
- Besteht Interesse der Zusammenarbeit?

## Interesse mitzuwirken? Bitte schreibt an m.drobisch(at)googlemail.com

Zusammen

## Danke für für die Aufmerksamkeit!

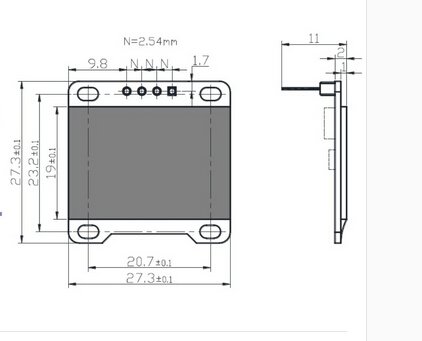
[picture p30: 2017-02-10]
hardware/terminal/Oled_drawing.jpg

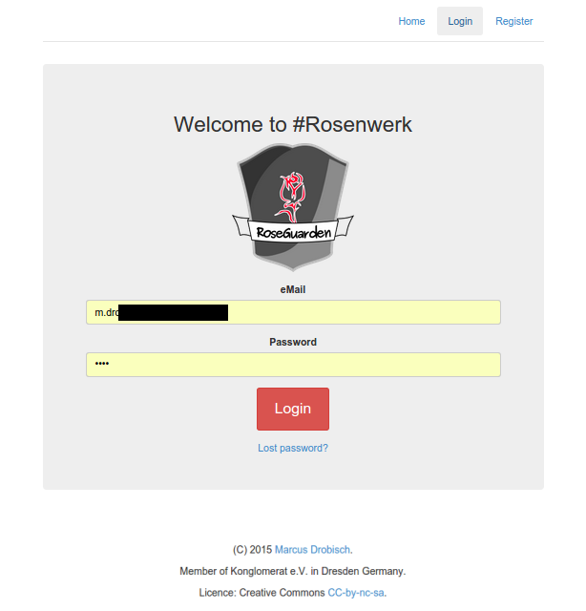
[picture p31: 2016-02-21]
documentation/screenshots/login.png

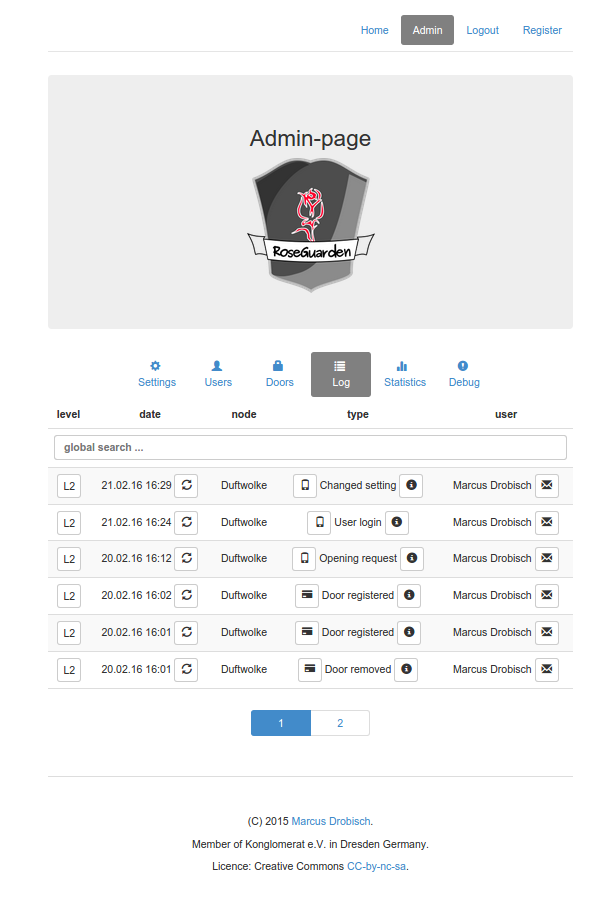
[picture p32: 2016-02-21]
documentation/screenshots/admin_log.png

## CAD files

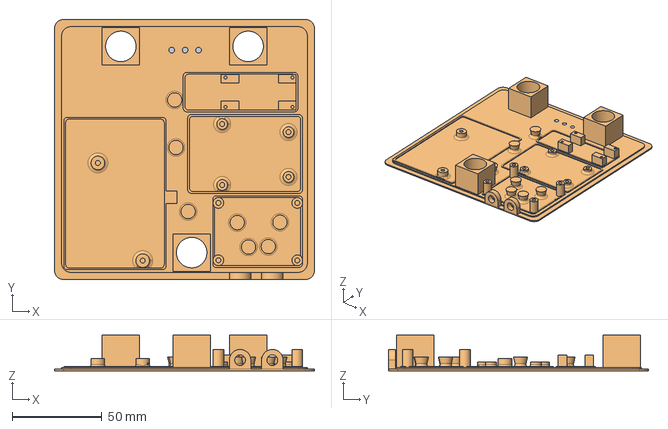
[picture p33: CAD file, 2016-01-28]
hardware/case/case_raspberryB_plate_v5.fcstd
145.0 x 145.0 x 19.8 mm
CasePocket

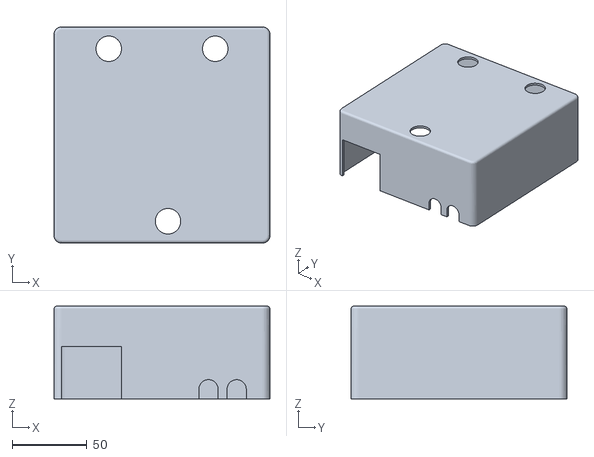
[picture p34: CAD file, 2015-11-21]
hardware/case/STL/raspB_cover_v1.stl
144.0 x 144.0 x 61.8

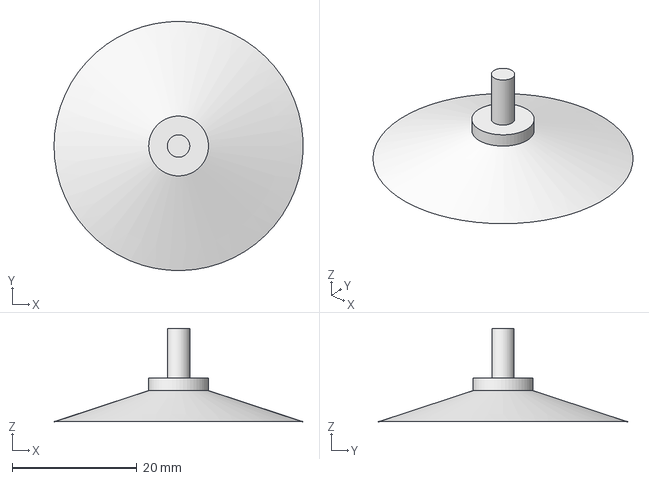
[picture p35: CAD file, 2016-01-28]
hardware/case2/Sucker.fcstd
40.0 x 40.0 x 15.0 mm

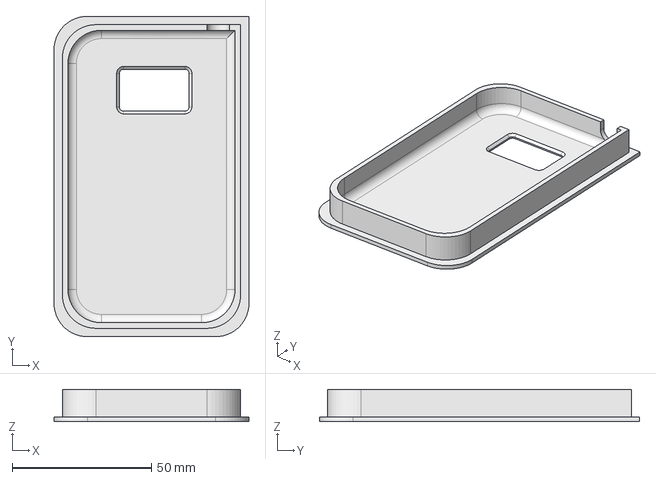
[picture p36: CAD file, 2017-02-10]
hardware/terminal/terminal_v2_cap.FCStd
70.0 x 115.0 x 11.6 mm

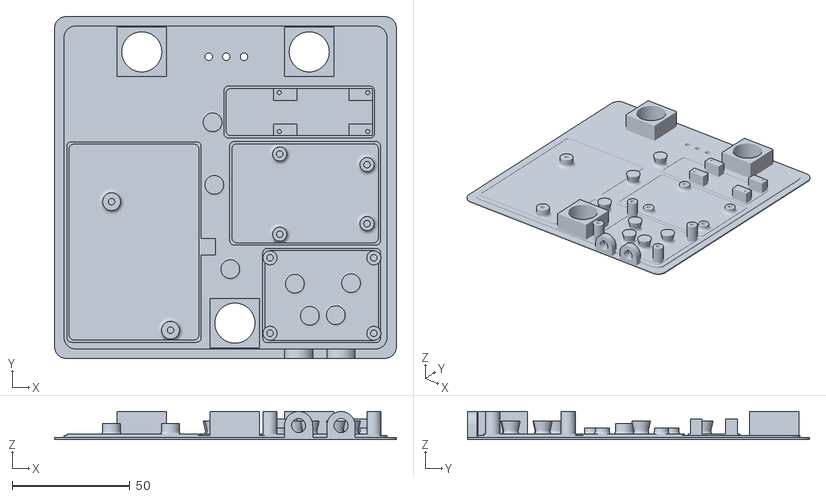
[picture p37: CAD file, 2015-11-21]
hardware/case/STL/rasp_plate_v5.stl
145.0 x 145.0 x 11.9

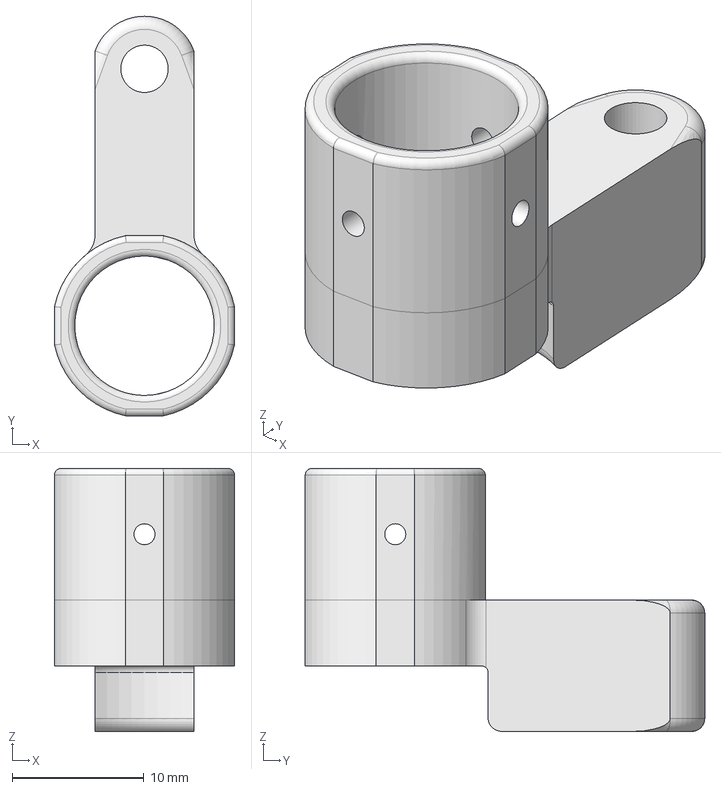
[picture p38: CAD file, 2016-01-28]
hardware/case2/SuckerHolder.fcstd
13.7 x 30.4 x 20.0 mm

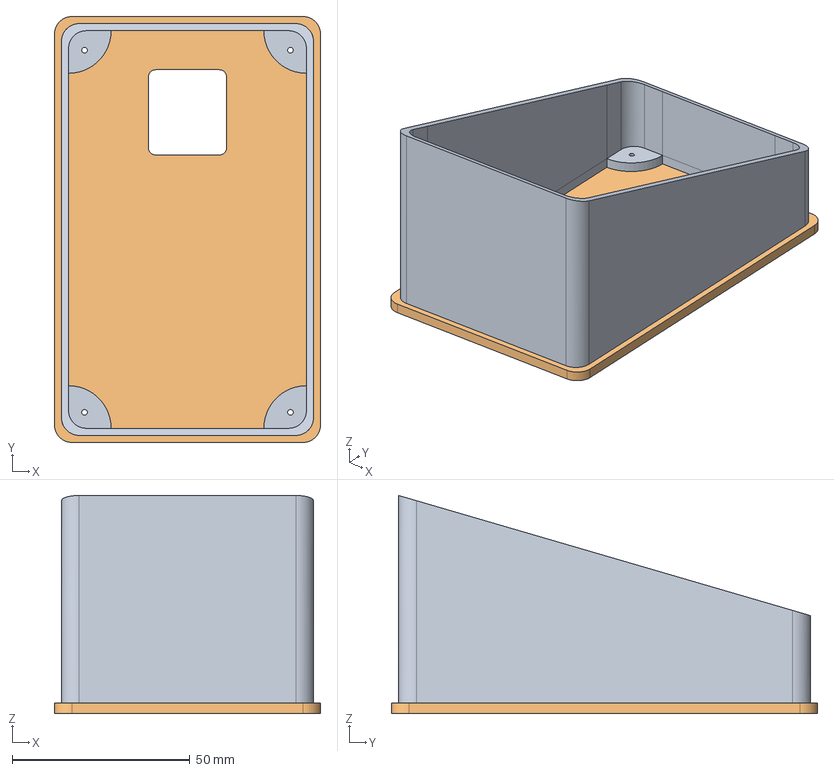
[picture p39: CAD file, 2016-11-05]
hardware/terminal/terminal_v1.FCStd
75.0 x 120.0 x 61.4 mm

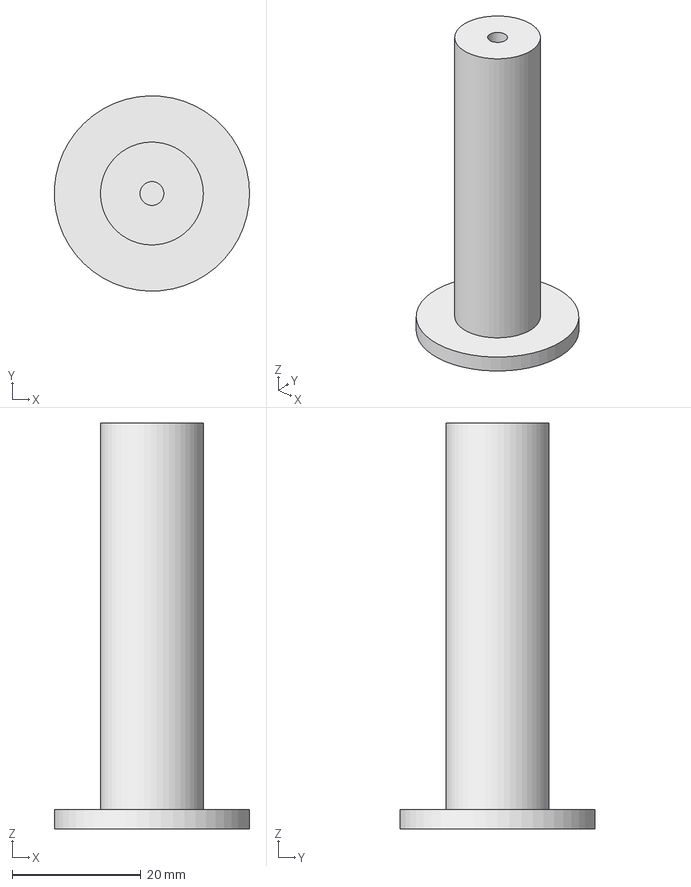
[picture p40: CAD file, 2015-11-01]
hardware/case/knob_20mm.fcstd
30.3 x 30.3 x 63.0 mm

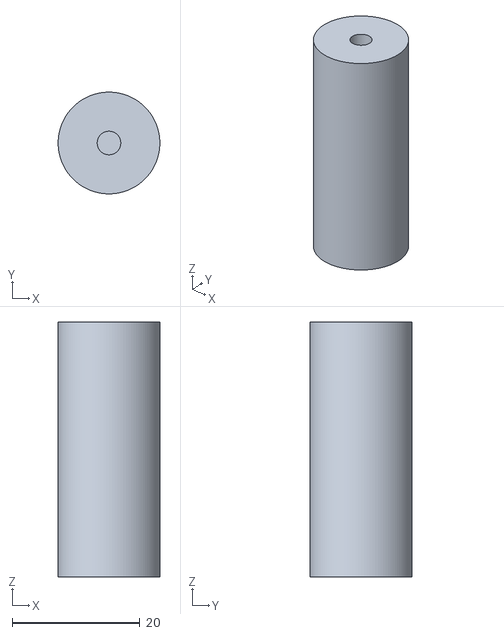
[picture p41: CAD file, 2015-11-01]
hardware/case/STL/knop_20mm_v2.stl
16.0 x 16.0 x 40.0

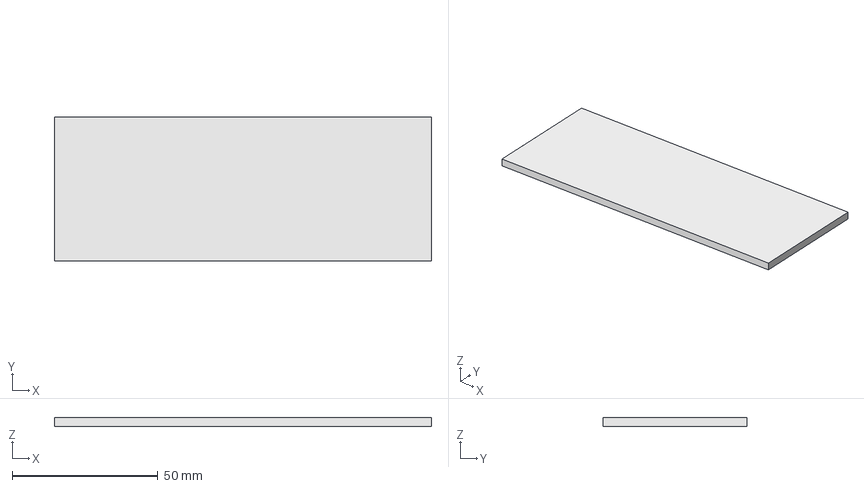
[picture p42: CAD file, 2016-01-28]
hardware/case2/Sidepanel.fcstd
129.5 x 49.5 x 3.00 mm

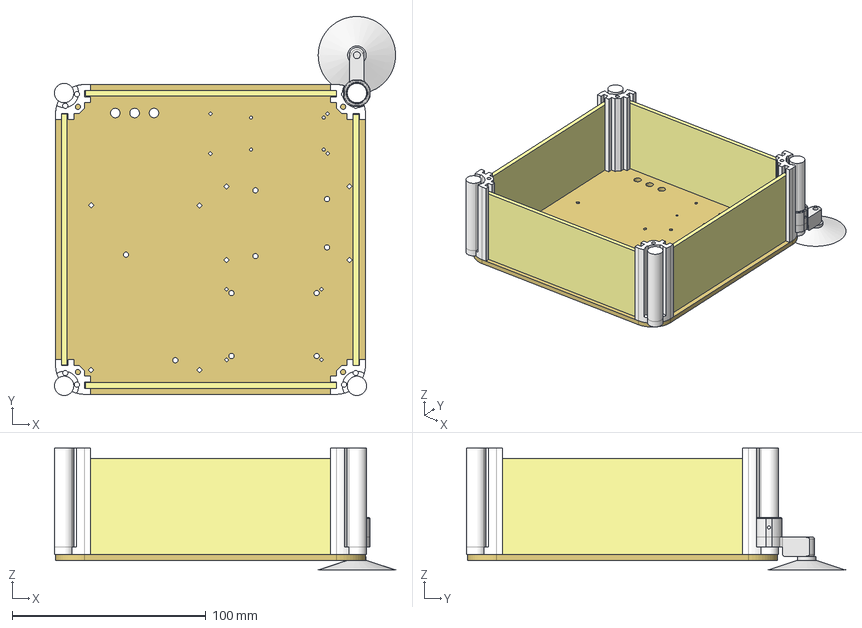
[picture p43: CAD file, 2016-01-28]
hardware/case2/Case.fcstd
176.2 x 195.7 x 63.0 mm
Board_01
Edge_01
Edge_02
Sidepanel_01
Edge_03
Edge_04
Sidepanel_02
Sidepanel_03
Sidepanel_04
SuckerHolder_01
Sucker_01

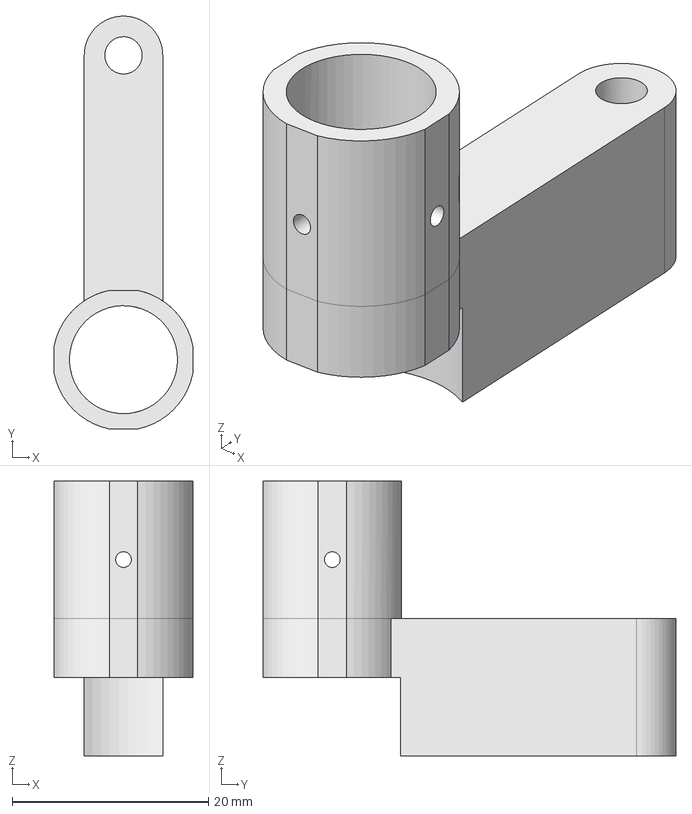
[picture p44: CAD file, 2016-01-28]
hardware/case2/SuckerHolder2.fcstd
14.1 x 42.0 x 28.0 mm

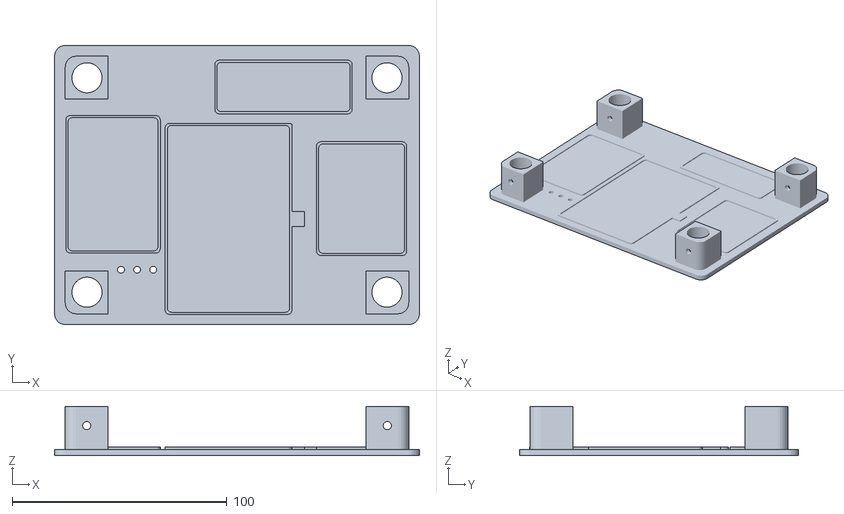
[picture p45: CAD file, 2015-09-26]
hardware/case/STL/test.stl
170.0 x 130.0 x 23.0

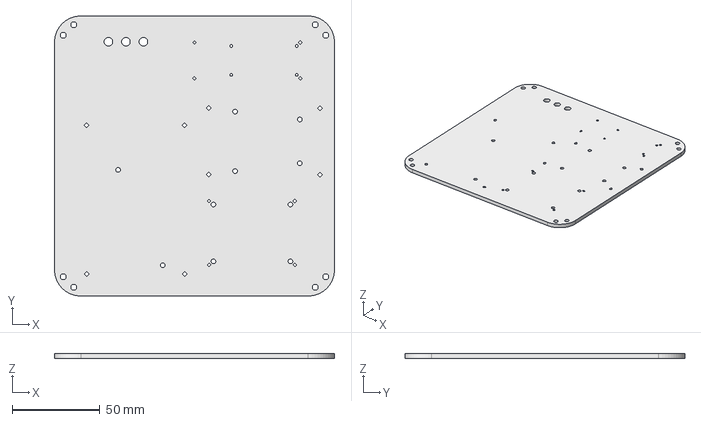
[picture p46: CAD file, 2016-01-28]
hardware/case2/Board.fcstd
160.0 x 160.0 x 3.00 mm

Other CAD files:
hardware/case/case_raspberryB_cover.fcstd
hardware/case2/Edge.fcstd
hardware/case/roseguarden_logo_constructed.fcstd
hardware/case/roseguarden_logo_svg_imported.fcstd
hardware/case/STL/knop_20mm_v1.stl
hardware/case/STL/rasp_plate_v4.stl
hardware/case/case_raspberryB_plate.fcstd
hardware/case/case_raspberryB_plate_v2.fcstd
hardware/case/case_raspberryB_plate_v3.fcstd
hardware/case/case_raspberryB_plate_v4.fcstd
hardware/case/roseguarden_logo_svg_imported.stl

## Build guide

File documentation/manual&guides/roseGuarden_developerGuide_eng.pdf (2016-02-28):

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

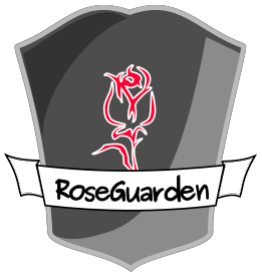
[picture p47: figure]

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

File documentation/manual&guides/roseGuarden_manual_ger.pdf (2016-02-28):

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

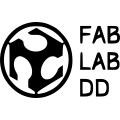
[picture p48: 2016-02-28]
documentation/manual&guides/images/FabLabDD.png

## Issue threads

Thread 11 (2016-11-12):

no rfid tag detected

sroesslhuemer, 2016-11-12:
welche moeglichkeiten habe ich rauszufinden warum kein tag erkannt wird < keine reaktion obwohl alles lt. schema verdrahtet

mdrobisch, 2016-11-12:
Hallo Siegi,
ich hatte dir am 9.11 geschrieben. Ist die Mail evt. im Spam gelandet?

SG
Marcus

sroesslhuemer, 2016-11-15:
hallo marcus,

...konnte inzwischen das problem orten und lösen (siehe unten)

- habe jetzt 2 voneinander unabhängige systeme - jetzt meine frage - was muss ich tun, um ein system zu haben ?

weiters - unter statistics sagt er mir dass evtl. ein parameter nicht gesetzt ist (umgebungsvariable?)

danke für die infos

#######################################
Make sure the SPI Interface is enabled:
Edit the file /boot/config.txt and add the following two lines:
device_tree_param=spi=on
dtoverlay=spi-bcm2708
Reboot the Pi and check if the SPI Interface software is running:
$ dmesg | grep spi
You should see something like:
[    8.577659] bcm2708_spi 20204000.spi: master is unqueued, this is deprecated
[    8.578491] bcm2708_spi 20204000.spi: SPI Controller at 0x20204000 (irq 80)
You can also check:
$ lsmod
which should list:
spi_bcm2708             5429  0_

sroesslhuemer, 2016-11-15:
hallo marcus,

...konnte inzwischen das problem orten und lösen (siehe unten)

    habe jetzt 2 voneinander unabhängige systeme - jetzt meine frage - was muss ich tun, um ein system zu haben ?

weiters - unter statistics sagt er mir dass evtl. ein parameter nicht gesetzt ist (umgebungsvariable?)

danke für die infos

#######################################
Make sure the SPI Interface is enabled:
Edit the file /boot/config.txt and add the following two lines:
device_tree_param=spi=on
dtoverlay=spi-bcm2708
Reboot the Pi and check if the SPI Interface software is running:
$ dmesg | grep spi
You should see something like:
[ 8.577659] bcm2708_spi 20204000.spi: master is unqueued, this is deprecated
[ 8.578491] bcm2708_spi 20204000.spi: SPI Controller at 0x20204000 (irq 80)
You can also check:
$ lsmod
which should list:
spi_bcm2708 5429 0_

mdrobisch, 2017-04-19:
Hallo Siegi,
Entschuldige die späte Antwort. Deine Nachricht ist leider nicht bei mir angekommen.
Läuft dein System mittlerweile oder gab es noch Probleme?

SG
Marcus

PS: Mit dem neuen Release 1.0.0 kommt ein Installer, der dir die Konfiguration abnimmt.

sroesslhuemer, 2017-04-20:
Hallo,

....nein läuft nur im single modus – wenn ich 2 zusammenhänge geht’s leider nicht

...wann kommt das neue release ? – und hilft es mir wenn ich mehrere schlösser zusammenhänge ?

Lg

siegi

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

mdrobisch, 2017-04-20:
Ja, das wird damit auch einfacher. Die IP des masters angeben und fertig. Ich hab da schon eine Idee, wie das funktionieren kann. Der Installer ist relativ einfach zu bedienen. Das 1.0.0 Release plane ich Ende Juni.

timo5500, 2019-05-10:
Hi,

ich habe das selbe problem ich kann aber mit den tests scripts die tags lesen aber das webinterface zeigt immer an No rfid-tag detected

Sico93, 2019-09-16:
@mdrobisch Ich habe leider auch noch das selbe Problem im Webinterface. Die Testskripte funktionieren alle, ich verstehe aber einfach nicht wieso die Website einfach keine Tags erkennt.
Ich bin scheinbar auch einfach nicht in der Lage herauszufinden welches Skript da abgerufen wird :( Ich würde mich über eine Antwort freuen, auch wenn das Projekt scheinbar tot gelaufen ist :/

mdrobisch, 2019-10-03:
Hallo Zusammen,
aufgrund tiefgreifender Probleme in der Architektur haben wir beschlossen, Roseguarden vollständig neu aufzusetzen. Wir arbeiten in einer Gruppe von 3 Personen am Nachfolger und werden keine Zeit mehr in die Pfelge der alten Version stecken. Sorry hierfür.
Die Neuauflage ist unter https://gitlab.com/roseguarden/roseguarden zu finden.

sroesslhuemer, 2019-10-04:
hallo,
...was heisst in diesem fall neu aufgesetzt ? - ist das eine kpl. neue hardware oder kann ich die alte hardware verwenden ?
lg

mdrobisch, 2019-10-14:
Hallo sroesslhuemer,
Kurz zusammengefasst soll es folgende Veränderungen geben.
- Verwaltung auf einen Server (nicht nur lokal), damit auch sichere Verwaltung über das Internet möglich wird (lokales Intranet über LAN wird ebenfalls weiterhin möglich sein). Der Prototyp ist hier zu finden https://roseguarden.fabba.space/dashboard
- Einen besseren Reader mit höherer Reichweite https://www.olimex.com/Products/Modules/RFID/MOD-RFID1356MIFARE/
- Optionales Display zur Anzeige des Status, vermutlich auch mit Zugang über 1-mal-Pins https://www.olimex.com/Products/Modules/LCD/MOD-LCD2-8RTP/open-source-hardware
- Unabhängigkeit von Lesegerät und z.B. Türöffner (Lesegerät in einem anderen Raum als der Türöffner) https://www.olimex.com/Products/IoT/ESP32/ESP32-EVB/open-source-hardware

Die alte Hardware kann ggf. wiederverwendet werden. Ich kann dabei gern unterstützen. Wir haben Adapterboard entwickelt, die kann ich gerne rausgeben.

Beste Grüße

-

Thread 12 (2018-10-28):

Payment

baskettal, 2018-10-28:
Hallo,

haben Sie vor, in der nächsten Zeit, das Paymentmodul zu implementieren, wie auf Ihrer Weseite beschrieben?

Beste Grüße!

mdrobisch, 2019-10-03:
Sorry für die späte Antwort.
Nach langer Inaktivität arbeiten wir nun an einem kompletten Remake von Roseguarden.
https://gitlab.com/roseguarden/roseguarden

Closed 2019-10-03.

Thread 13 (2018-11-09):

RoseGuarden for two or three doors?

andreaconklin01, 2018-11-09:
Can I use the RoseGuarden system for two or three doors with just one raspberry pi?

mdrobisch, 2019-10-03:
At the moment ther is no plan to make further updates to roseguarden.
We are working on a complete rework under https://gitlab.com/roseguarden/roseguarden.

Closed 2019-10-03.

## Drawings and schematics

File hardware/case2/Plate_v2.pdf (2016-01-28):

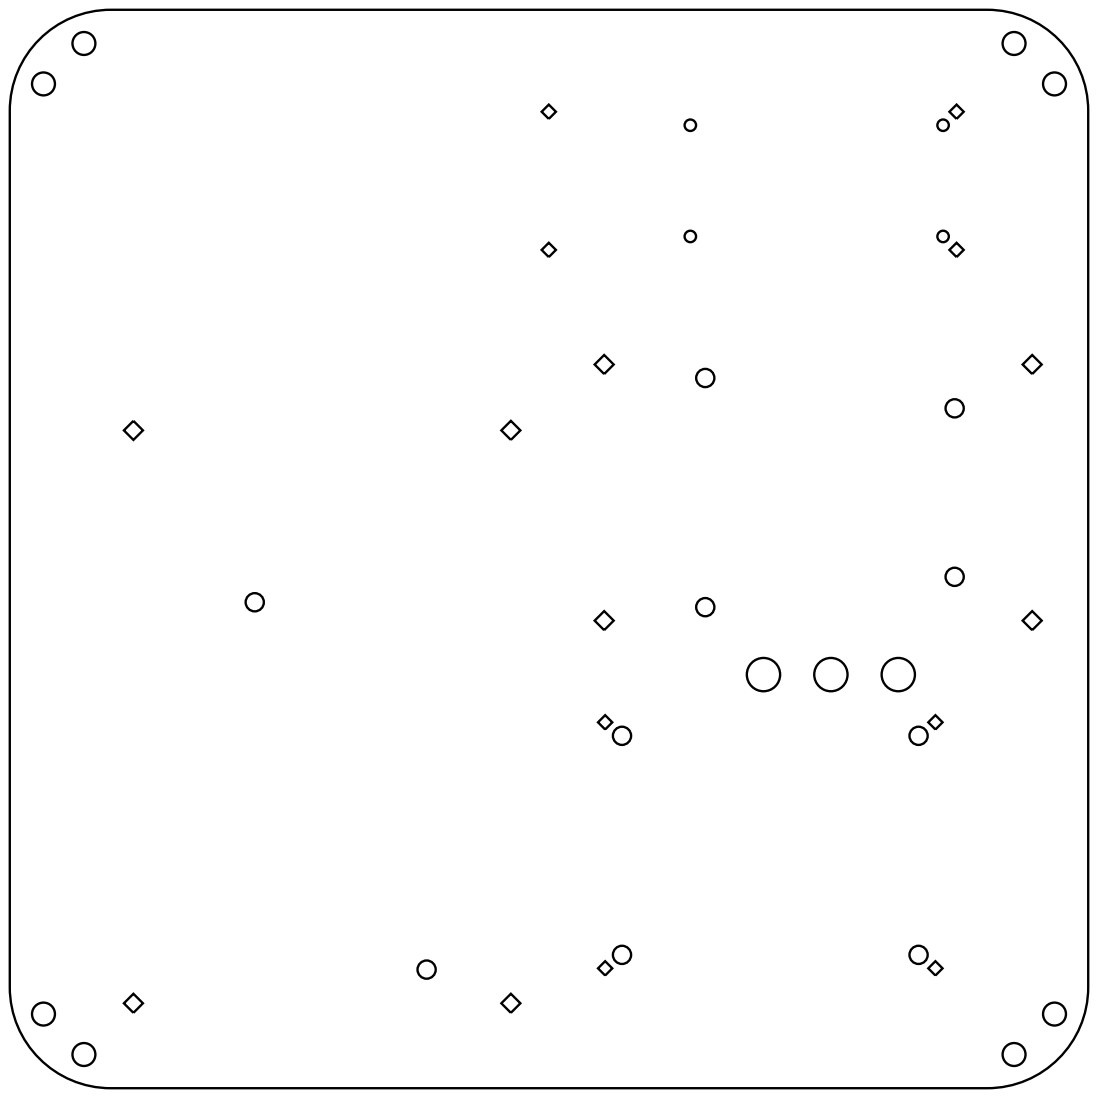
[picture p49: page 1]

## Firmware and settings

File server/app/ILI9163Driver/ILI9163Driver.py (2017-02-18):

#!/usr/bin/env python
# -*- coding: utf-8 -*-

#
#   (1) Based on the ILI9163 Library of BLavery https://github.com/BLavery/LIBtft144
#   (2) Which based on ILI9163 128x128 LCD library   - parallel I/O AVR C code
#      Copyright (C) 2012 Simon Inns    Email: simon.inns@gmail.com
#      http://www.waitingforfriday.com/index.php/Reverse_Engineering_a_1.5_inch_Photoframe
#   (3) ... then based on Antares python/parallel Raspberry Pi code:
#      http://www.raspberrypi.org/forums/viewtopic.php?t=58291&p=450201
#   (4) ... making this version lib_tft144 python SPI interface for RPI or Virtual GPIO
#      (It's looking a bit different now from Inns' original!)
#
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


# 128x128 pixels,
# Note the board is write-only. There is no feedback if board is absent or misbehaving.

import sys

if __name__ == '__main__':
    print (sys.argv[0], 'is an importable module:')
    print ("...  from", sys.argv[0], "import TFT144")
    exit()

from time import sleep
import os
GPIO = None

TFTWIDTH    = 130
TFTHEIGHT   = 131

#ILI9163 commands
NOP=0x00
SOFT_RESET=0x01
ENTER_SLEEP_MODE=0x10
EXIT_SLEEP_MODE=0x11
ENTER_PARTIAL_MODE=0x12
ENTER_NORMAL_MODE=0x13
EXIT_INVERT_MODE=0x20
ENTER_INVERT_MODE=0x21
SET_GAMMA_CURVE=0x26
SET_DISPLAY_OFF=0x28
SET_DISPLAY_ON=0x29
SET_COLUMN_ADDRESS=0x2A
SET_PAGE_ADDRESS=0x2B
WRITE_MEMORY_START=0x2C
SET_PARTIAL_AREA=0x30
SET_SCROLL_AREA=0x33
SET_ADDRESS_MODE=0x36
SET_SCROLL_START=0X37
EXIT_IDLE_MODE=0x38
ENTER_IDLE_MODE=0x39
SET_PIXEL_FORMAT=0x3A
WRITE_MEMORY_CONTINUE=0x3C
READ_MEMORY_CONTINUE=0x3E
FRAME_RATE_CONTROL1=0xB1
FRAME_RATE_CONTROL2=0xB2
FRAME_RATE_CONTROL3=0xB3
DISPLAY_INVERSION=0xB4
POWER_CONTROL1=0xC0
POWER_CONTROL2=0xC1
POWER_CONTROL3=0xC2
POWER_CONTROL4=0xC3
POWER_CONTROL5=0xC4
VCOM_CONTROL1=0xC5
VCOM_CONTROL2=0xC6
VCOM_OFFSET_CONTROL=0xC7
POSITIVE_GAMMA_CORRECT=0xE0
NEGATIVE_GAMMA_CORRECT=0xE1
GAM_R_SEL=0xF2

VIRTUALGPIO = 0

class ILI9163Driver:
    # red board is built 180 rotated relative to black board !!
    ORIENTATION0=0
    ORIENTATION90=96
    ORIENTATION270=160
    ORIENTATION180=192
    # Do you rotate the image, or the device?  :-)

    def __init__(self, gpio, spidev, CE, dc_pin, rst_pin=0, led_pin=0, orientation=ORIENTATION0, isRedBoard=False, spi_speed=16000000):
        # CE is 0 or 1 for RPI, but is actual CE pin for virtGPIO
        # RST pin.  0  means soft reset (but reset pin still needs holding high (3V)
        # LED pin, may be tied to 3V (abt 14mA) or used on a 3V logic pin (abt 7mA)
        # and this object needs to be told the GPIO and SPIDEV objects to talk to
        global GPIO
        GPIO = gpio
        self.SPI = spidev
        self.orientation = orientation
        self.is_redboard = isRedBoard
        self.BLUE = self.colour565(0,0,255)
        self.GREEN = self.colour565(0,255, 0)
        self.RED = self.colour565(255,0,0)
        self.PINK = self.colour565(255,120,120)
        self.LIGHTBLUE = self.colour565(120,120,255)
        self.LIGHTGREEN = self.colour565(120,255,120)
        self.BLACK = self.colour565(0,0,0)
        self.WHITE = self.colour565(255,255,255)
        self.GREY = self.colour565(120,120,120)
        self.YELLOW = self.colour565(255,255,0)
        self.MAGENTA = self.colour565(255,0,255)
        self.CYAN = self.colour565(0,255,255)

        self.RST = rst_pin
        self.DC = dc_pin
        self.LED = led_pin
        GPIO.setup(dc_pin, GPIO.OUT)
        GPIO.output(dc_pin, GPIO.HIGH)
        if rst_pin:
            GPIO.setup(rst_pin, GPIO.OUT)
            GPIO.output(rst_pin, GPIO.HIGH)
        if led_pin:
            GPIO.setup(led_pin, GPIO.OUT)
            self.led_on(True)
        self.SPI.open(0, CE)    # CE is 0 or 1   (means pin CE0 or CE1) or actual CE pin for virtGPIO
        self.SPI.max_speed_hz=spi_speed
        # Black board may cope with 32000000 Hz. Red board up to 16000000. YMMV.
        sleep(0.5)
        self.init_LCD(orientation)

    def led_on(self, onoff):
        if self.LED:
            GPIO.output(self.LED, GPIO.HIGH if onoff else GPIO.LOW)

    #function to pack 3 bytes of rgb value in 2 byte integer, R,G and B 0-255
    def colour565(self, r,g,b):
       return ((b & 0xF8) << 8) | ((g & 0xFC) << 3) | (r >> 3)

    #functions to translate x,y pixel coords. to text column,row
    def textX(self, x, font=3):
       return x*(self.fontDim[font][0])

    def textY(self, y, font=3):
       return y*(self.fontDim[font][1])

    #initial LCD reset
    def reset_LCD(self):
       if self.RST == 0:
           self.write_command(SOFT_RESET)
       else:
           GPIO.output(self.RST,False)
           sleep (0.2)
           GPIO.output(self.RST,True)
       sleep (0.2)
       return

    #write command to controller
    def write_command(self, address):
       GPIO.output(self.DC,False)
       self.SPI.writebytes([address])


    #write data
    def write_data(self, data):
       GPIO.output(self.DC,True)
       if not type(data) == type([]):   # is it already a list?
            data = [data]
       self.SPI.writebytes(data)

    #-------------------------------------------

    def init_LCD(self, orientation):
       self.reset_LCD()
       self.write_command(EXIT_SLEEP_MODE)
       sleep(0.05)
       self.write_command(SET_PIXEL_FORMAT)
       self.write_data(0x05)
       self.write_command(SET_GAMMA_CURVE)
       self.write_data(0x04)
       self.write_command(GAM_R_SEL)
       self.write_data(0x01)

       self.write_command(POSITIVE_GAMMA_CORRECT)
       self.write_data([0x3f, 0x25, 0x1c, 0x1e, 0x20, 0x12, 0x2a, 0x90, 0x24, 0x11, 0, 0, 0, 0, 0])

       self.write_command(NEGATIVE_GAMMA_CORRECT)
       self.write_data([0x20, 0x20, 0x20, 0x20, 0x05, 0, 0x15, 0xa7, 0x3d, 0x18, 0x25, 0x2a, 0x2b, 0x2b, 0x3a])
       self.write_command(FRAME_RATE_CONTROL1)
       self.write_data([0x08, 0x08])

       self.write_command(DISPLAY_INVERSION)
       self.write_data(0x01)

       self.write_command(POWER_CONTROL1)
       self.write_data([0x0a, 0x02])

       self.write_command(POWER_CONTROL2)
       self.write_data(0x02)

       self.write_command(VCOM_CONTROL1)
       self.write_data([0x50, 0x5b])

       self.write_command(VCOM_OFFSET_CONTROL)
       self.write_data(0x40)
       self.set_frame()

       self.write_command(SET_ADDRESS_MODE)
       self.write_data(orientation)

       self.clear_display(self.BLACK)
       self.write_command(SET_DISPLAY_ON)
    #   self.write_command(WRITE_MEMORY_START)

    # clear display,writes same color pixel in all screen
    def clear_display(self, color):
       color_hi=color>>8
       color_lo= color&(~(65280))
       self.set_frame()
       self.write_command(WRITE_MEMORY_START)
       if GPIO.RPI_REVISION == VIRTUALGPIO:
           GPIO.output(self.DC,True)
           self.SPI.fill(16384, color)
           # For virtGPIO "fill" is MUCH faster, but is a special VirtGPIO function
       else:
           # Otherwise (RPI) repetitively push out all those identical pixels
           for row in range(TFTHEIGHT):
                self.write_data([color_hi, color_lo] * TFTWIDTH)

    def set_frame(self, x1=0, x2=TFTWIDTH-1, y1=0, y2=TFTHEIGHT-1 ):
        if self.is_redboard:
           if self.orientation==self.ORIENTATION0:
               y1 += 32
               y2 += 32
           if self.orientation==self.ORIENTATION90:
               x1 += 32
               x2 += 32
        self.write_command(SET_COLUMN_ADDRESS)
        self.write_data([0, x1, 0, x2])
        self.write_command(SET_PAGE_ADDRESS)
        self.write_data([0, y1, 0, y2])

    # draw a dot in x,y with 'color' colour
    def draw_dot(self, x,y,color):
       color_hi=color>>8
       color_lo= color&(~(65280))
       self.set_frame(x, x+1, y, y+1)
       self.write_command(WRITE_MEMORY_START)
       self.write_data([color_hi,color_lo])

    # Bresenham's algorithm to draw a line with integers
    # x0<=x1, y0<=y1
    def draw_line(self, x0,y0,x1,y1,color):
       dy=y1-y0
       dx=x1-x0
       if (dy<0):
          dy=-dy
          stepy=-1
       else:
          stepy=1
       if (dx<0):
          dx=-dx
          stepx=-1
       else:
          stepx=1
       dx <<=1
       dy <<=1
       self.draw_dot(x0,y0,color)
       if (dx>dy):
          fraction=dy-(dx>>1)
          while (x0!=x1):
             if (fraction>=0):
                y0 +=stepy
                fraction -=dx
             x0 +=stepx
             fraction +=dy
             self.draw_dot(x0,y0,color)
       else:
          fraction=dx-(dy>>1)
          while (y0!=y1):
             if (fraction>=0):
                x0 +=stepx
                fraction -=dy
             y0 +=stepy
             fraction +=dx
             self.draw_dot(x0,y0,color)

    # draws hollow rectangle
    # x0<=x1, y0<= y1
    def draw_rectangle(self, x0,y0,x1,y1,color):
       self.draw_line(x0,y0,x0,y1,color)
       self.draw_line(x0,y1,x1,y1,color)
       self.draw_line(x1,y0,x1,y1,color)
       self.draw_line(x0,y0,x1,y0,color)

    # draws filled rectangle, fills frame memory section with same pixel
    # x0<=x1, y0<=y1
    def draw_filled_rectangle(self, x0,y0,x1,y1,color):
       color_hi=color>>8
       color_lo= color&(~(65280))
       self.set_frame(x0, x1, y0, y1)

       self.write_command(WRITE_MEMORY_START)
       for pixels in range (0,(1+x1-x0)):
            dbuf = [color_hi, color_lo] * (y1-y0)
            self.write_data(dbuf)

    #Bresenham's circle algorithm, circle can't pass screen boundaries
    def draw_circle(self, x0,y0,radio,color):
       error=1-radio
       errorx=1
       errory=-2*radio
       y=radio
       x=0
       self.draw_dot(x0,y0+radio,color)
       self.draw_dot(x0,y0-radio,color)
       self.draw_dot(x0+radio,y0,color)
       self.draw_dot(x0-radio,y0,color)
       while (x<y):
          if (error>=0):
             y -=1
             errory +=2
             error +=errory
          x +=1
          errorx +=2
          error +=errorx
          self.draw_dot(x0+x,y0+y,color)
          self.draw_dot(x0-x,y0+y,color)
          self.draw_dot(x0+x,y0-y,color)
          self.draw_dot(x0-x,y0-y,color)
          self.draw_dot(x0+y,y0+x,color)
          self.draw_dot(x0-y,y0+x,color)
          self.draw_dot(x0+y,y0-x,color)
          self.draw_dot(x0-y,y0-x,color)


    def draw_image(self, image,x0=0,y0=0):
        pix = image.load()
        w = image.size[0]
        h = image.size[1]
        self.set_frame(x0, x0 + w - 1, y0, y0 + h - 1)
        self.write_command(WRITE_MEMORY_START)
        for y in range(h):
            dbuf = [0] * (w * 2)
            for x in range(w):
                pixel = pix[x, y]
                r = pixel[0]
                g = pixel[1]
                b = pixel[2]
                RGB = self.colour565(r, g, b)
                # RGB = self.YELLOW
                dbuf[2 * x] = RGB >> 8
                dbuf[1 + (2 * x)] = RGB & (~65280)
            self.write_data(dbuf)

        return True

    def draw_bmp(self, filename, x0=0, y0=0):
        if not os.path.exists(filename):
            return False
        with open(filename, 'rb') as bitmap_file:
            bitmap_file.seek(18)
            w = ord(bitmap_file.read(1))
            bitmap_file.seek(22)
            h = ord(bitmap_file.read(1))
            bitmap_file.seek(10)
            start = ord(bitmap_file.read(1))
            bitmap_file.seek(start)
            self.set_frame(x0, x0+w-1, y0, y0+h-1)
            self.write_command(WRITE_MEMORY_START)
            for y in range(h):   # 3 bytes of colour / pixel
                  dbuf = [0] * (w*2)
                  for x in range(w):
                      b = ord(bitmap_file.read(1))
                      g = ord(bitmap_file.read(1))
                      r = ord(bitmap_file.read(1))
                      RGB = self.colour565(r, g, b)
                      #RGB = self.YELLOW
                      dbuf[2*x] = RGB>>8
                      dbuf[1 + (2*x)] = RGB&(~65280)
                  self.write_data(dbuf)
                  # Now, BMP has a 4byte alignment issue at end of each line   V1.0.1
                  x = 3*w # bytes in line @ 3bytes/pixel
                  while (x % 4):
                      x += 1
                      bitmap_file.read(1)   # waste a byte until aligned
        return True

    def invert_screen(self):
       self.write_command(ENTER_INVERT_MODE)

    def normal_screen(self):
       self.write_command(EXIT_INVERT_MODE)


########################################################################

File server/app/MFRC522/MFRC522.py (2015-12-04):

#!/usr/bin/env python
# -*- coding: utf8 -*-

import RPi.GPIO as GPIO
import spi
import signal
import time
  
class MFRC522:
  NRSTPD = 22
  
  MAX_LEN = 16
  
  PCD_IDLE       = 0x00
  PCD_AUTHENT    = 0x0E
  PCD_RECEIVE    = 0x08
  PCD_TRANSMIT   = 0x04
  PCD_TRANSCEIVE = 0x0C
  PCD_RESETPHASE = 0x0F
  PCD_CALCCRC    = 0x03
  
  PICC_REQIDL    = 0x26
  PICC_REQALL    = 0x52
  PICC_ANTICOLL  = 0x93
  PICC_SElECTTAG = 0x93
  PICC_AUTHENT1A = 0x60
  PICC_AUTHENT1B = 0x61
  PICC_READ      = 0x30
  PICC_WRITE     = 0xA0
  PICC_DECREMENT = 0xC0
  PICC_INCREMENT = 0xC1
  PICC_RESTORE   = 0xC2
  PICC_TRANSFER  = 0xB0
  PICC_HALT      = 0x50
  
  MI_OK       = 0
  MI_NOTAGERR = 1
  MI_ERR      = 2
  
  Reserved00     = 0x00
  CommandReg     = 0x01
  CommIEnReg     = 0x02
  DivlEnReg      = 0x03
  CommIrqReg     = 0x04
  DivIrqReg      = 0x05
  ErrorReg       = 0x06
  Status1Reg     = 0x07
  Status2Reg     = 0x08
  FIFODataReg    = 0x09
  FIFOLevelReg   = 0x0A
  WaterLevelReg  = 0x0B
  ControlReg     = 0x0C
  BitFramingReg  = 0x0D
  CollReg        = 0x0E
  Reserved01     = 0x0F
  
  Reserved10     = 0x10
  ModeReg        = 0x11
  TxModeReg      = 0x12
  RxModeReg      = 0x13
  TxControlReg   = 0x14
  TxAutoReg      = 0x15
  TxSelReg       = 0x16
  RxSelReg       = 0x17
  RxThresholdReg = 0x18
  DemodReg       = 0x19
  Reserved11     = 0x1A
  Reserved12     = 0x1B
  MifareReg      = 0x1C
  Reserved13     = 0x1D
  Reserved14     = 0x1E
  SerialSpeedReg = 0x1F
  
  Reserved20        = 0x20  
  CRCResultRegM     = 0x21
  CRCResultRegL     = 0x22
  Reserved21        = 0x23
  ModWidthReg       = 0x24
  Reserved22        = 0x25
  RFCfgReg          = 0x26
  GsNReg            = 0x27
  CWGsPReg          = 0x28
  ModGsPReg         = 0x29
  TModeReg          = 0x2A
  TPrescalerReg     = 0x2B
  TReloadRegH       = 0x2C
  TReloadRegL       = 0x2D
  TCounterValueRegH = 0x2E
  TCounterValueRegL = 0x2F
  
  Reserved30      = 0x30
  TestSel1Reg     = 0x31
  TestSel2Reg     = 0x32
  TestPinEnReg    = 0x33
  TestPinValueReg = 0x34
  TestBusReg      = 0x35
  AutoTestReg     = 0x36
  VersionReg      = 0x37
  AnalogTestReg   = 0x38
  TestDAC1Reg     = 0x39
  TestDAC2Reg     = 0x3A
  TestADCReg      = 0x3B
  Reserved31      = 0x3C
  Reserved32      = 0x3D
  Reserved33      = 0x3E
  Reserved34      = 0x3F
    
  serNum = []
  
  def __init__(self, dev='/dev/spidev0.0', spd=1000000):
    spi.openSPI(device=dev,speed=spd)
    GPIO.setmode(GPIO.BOARD)
    GPIO.setup(22, GPIO.OUT)
    GPIO.output(self.NRSTPD, 1)
    self.MFRC522_Init()
  
  def MFRC522_Reset(self):
    self.Write_MFRC522(self.CommandReg, self.PCD_RESETPHASE)
  
  def Write_MFRC522(self, addr, val):
    spi.transfer(((addr<<1)&0x7E,val))
  
  def Read_MFRC522(self, addr):
    val = spi.transfer((((addr<<1)&0x7E) | 0x80,0))
    return val[1]
  
  def SetBitMask(self, reg, mask):
    tmp = self.Read_MFRC522(reg)
    self.Write_MFRC522(reg, tmp | mask)
    
  def ClearBitMask(self, reg, mask):
    tmp = self.Read_MFRC522(reg);
    self.Write_MFRC522(reg, tmp & (~mask))
  
  def AntennaOn(self):
    temp = self.Read_MFRC522(self.TxControlReg)
    if(~(temp & 0x03)):
      self.SetBitMask(self.TxControlReg, 0x03)
  
  def AntennaOff(self):
    self.ClearBitMask(self.TxControlReg, 0x03)
  
  def MFRC522_ToCard(self,command,sendData):
    backData = []
    backLen = 0
    status = self.MI_ERR
    irqEn = 0x00
    waitIRq = 0x00
    lastBits = None
    n = 0
    i = 0
    
    if command == self.PCD_AUTHENT:
      irqEn = 0x12
      waitIRq = 0x10
    if command == self.PCD_TRANSCEIVE:
      irqEn = 0x77
      waitIRq = 0x30
    
    self.Write_MFRC522(self.CommIEnReg, irqEn|0x80)
    self.ClearBitMask(self.CommIrqReg, 0x80)
    self.SetBitMask(self.FIFOLevelReg, 0x80)
    
    self.Write_MFRC522(self.CommandReg, self.PCD_IDLE);  
    
    while(i<len(sendData)):
      self.Write_MFRC522(self.FIFODataReg, sendData[i])
      i = i+1
    
    self.Write_MFRC522(self.CommandReg, command)
      
    if command == self.PCD_TRANSCEIVE:
      self.SetBitMask(self.BitFramingReg, 0x80)
    
    i = 2000
    while True:
      n = self.Read_MFRC522(self.CommIrqReg)
      i = i - 1
      if ~((i!=0) and ~(n&0x01) and ~(n&waitIRq)):
        break
    
    self.ClearBitMask(self.BitFramingReg, 0x80)
  
    if i != 0:
      if (self.Read_MFRC522(self.ErrorReg) & 0x1B)==0x00:
        status = self.MI_OK

        if n & irqEn & 0x01:
          status = self.MI_NOTAGERR
      
        if command == self.PCD_TRANSCEIVE:
          n = self.Read_MFRC522(self.FIFOLevelReg)
          lastBits = self.Read_MFRC522(self.ControlReg) & 0x07
          if lastBits != 0:
            backLen = (n-1)*8 + lastBits
          else:
            backLen = n*8
          
          if n == 0:
            n = 1
          if n > self.MAX_LEN:
            n = self.MAX_LEN
    
          i = 0
          while i<n:
            backData.append(self.Read_MFRC522(self.FIFODataReg))
            i = i + 1;
      else:
        status = self.MI_ERR
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

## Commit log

2015-08-23 bugfix(doc): remove personal data from screenshots
    [models.py]
2015-09-13 core(case): add preliminary case for raspberry pi B (old) for printing (freecad models)
    [case_raspberryB_cover.fcstd, case_raspberryB_plate.fcstd]
2015-09-13 feat(case): add bolts for cover-mounting, holes for led and holes for the suckers
    [case_raspberryB_plate.fcstd]
2015-09-26 feat(hardware): add final and former versions of the board-plate-model for FreeCAD and STL
    [case_raspberryB_plate.fcstd, case_raspberryB_plate_v2.fcstd, case_raspberryB_plate_v3.fcstd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]
2015-09-26 feature(readme): add documentation for assembly and modelling
2015-09-26 bugfix(redme): fix some typos and add more accurate informations for dimensions and bom
2015-09-27 feature(core): replace all placeholder-variable in the user profile with REST-api content. Implemented angular filter for cleaner display code-style. Add missing variables in the API-Model and the da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
    [models.py, serializers.py]
2015-09-29 feature(readme): add photos of the hardware and include a first BOM
2015-10-04 core(rfid): add SPI-Py and MFRC522_python libaries to the app
2015-10-10 feature(core): prepare to switch from dummy to API user-view on the admin page, rename frontend-dummy-names and add prototype for UserList-request to API
2015-10-11 feat(doc): add routing schematic for roseGuarden
2015-10-15 feature(frontend): switch from the slow python SimpleHTTPServer to the faster nodejs http-server
2015-10-15 feature(core): replace dummy user-list in admin-section with API-content, add additional modal for user access setup
    [models.py, serializers.py]
2015-10-18 fix(core): fix python-package dependencies for MFRC522
    [RFID.py]
2015-10-18 fix(dependencies): add fix for the spi-problem with kernel 3.18 and above, to the documentation (in new troubleshooting section)
2015-10-18 fix(doc): fix some typos in the readme-doc
    [worker.py]
2015-10-18 fix(core): disable flask debug to speed up the request-reply
    [config.py, worker.py]
2015-10-18 fix(core): take out debug-work-around
    [worker.py]
2015-10-19 IMPROVE (frontend) door-admin-section replaced dummy-content with REST-API request
    [serializers.py, worker.py]
2015-10-22 ADD (hardware) knub for secure the suckers
    [knob_20mm.fcstd, knop_20mm_v1.stl]
2015-10-22 FIX (core): background-worker save tagID in wrong structure
    [worker.py]
2015-11-01 FIX (preconfig): fix preconifg ip-addresses for doors
    [models.py, worker.py]
2015-11-01 IMPROVE (hardware): change case-holder-knop (version 2)
    [knob_20mm.fcstd, knop_20mm_v2.stl]
2015-11-21 ADD (hardware) constructions and 3d-object of raspberryB-cover (v1) and new raspberryB-plate design (v5)
    [case_raspberryB_cover.fcstd, case_raspberryB_plate_v5.fcstd, raspB_cover_v1.stl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]
2015-11-21 FIX (backend) to many details while rfid-reading
    [MFRC522.py, views.py]
2015-11-21 FIX (backend) to many detail on log on rfid-read
    [worker.py]
2015-11-22 ADD (backend) checking authentificaion after card-ID is read succesfully. Set relay for granted access
2015-11-22 FIX (backend) missing MFRC522_Request durign rfid-assign
    [worker.py]
2015-11-29 IMPROVE (backend) logging mechanism for internal events by having a dictionary to enable and disable "print"-log while running roseGuarden
2015-12-03 ADD (backend) nodenameto config and replace all old placeholder 'Test door' to the config from the config-file
    [config.py, views.py]
2015-12-04 FIX (backend) incorrect error warning and lock-dead problem
    [worker.py]
2015-12-04 FIX (backend) wrong key assign while rfid-assign
    [worker.py]
2015-12-04 FIX (backend) to fast retry for locking mechanism
    [worker.py]
2015-12-04 FIX (backend) problem with reference-secret generation
    [worker.py]
2015-12-04 IMPROVE (backend) error handling on rfid-based routines by adding try-catch-clauses and unlock the rfid-device
    [worker.py]
2015-12-04 FIX (backend) another wrong error-warning
    [worker.py]
2015-12-04 FIX (backend) problem of authentication of RFID-tag just after checkRfidTag
    [worker.py]
2015-12-04 IMPROVE (backend) anticolling rfid-tags in 3 attempts before error
    [worker.py]
2015-12-04 FIX (backend) bug that often rfid are not detected well
    [worker.py]
2015-12-04 FIX (backend) problems with detecting a rfid-tag again
    [worker.py]
2015-12-04 FIX (backend) problems with authentification while withdrawing again
    [worker.py]
2015-12-31 FIX (backend) some typos in the log
    [views.py, worker.py]
2015-12-31 ADD+FIX (backend) accessDayCyclicBudget to user-model and fix some typos and missing display-text
    [models.py, serializers.py, worker.py]
2015-12-31 FIX (backend) update actions only for nodes configured as master to prevent actions treated twice
    [worker.py]
2016-01-02 FIX (backend) to many warning for locked-spi device while DEBUG = TRUE
    [worker.py]
2016-01-15 ADD (backend) init. of leds and push green led if relay activated
2016-01-15 ADD (backend) additional led states
2016-01-15 ADD (backend) fasten up timer interval from 1.5s to 0.5s and adapt timer values
2016-01-15 FIX (backend) insynch. led timer
    [worker.py]
2016-01-15 REVERT (backend) last commit to change led timer synch.
    [worker.py]
2016-01-15 FIX (backup) cycle of timers
    [worker.py]
2016-01-28 ADD (hardware) new version 2 of a raspberry model b v1
    [Board.fcstd, Case.fcstd, Edge.fcstd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]
2016-01-29 ADD (doc) template for supervisord config and add some information to use it in the gloabl Readme.md.
    [supervisord.config.txt]
2016-02-02 ADD (frontend) lost authorization-card button, by now without functionality
2016-02-02 ADD (frontend) role of user in the profile view with angular-filter
2016-02-04 ADD (frontend+backend) possibility to invalidate rfid tag. By the user with a "Lost it" button or by the admins with a "Invalidate" menu entry. Close Feature issue #47 .
    [serializers.py, views.py]
2016-02-06 FIX (backend) bug #52 by adding catch of exceptions and logging them (database)
    [worker.py]
2016-02-06 IMPROVE (backend) bugfix of #52 by additional checking of empty array
    [worker.py]
2016-02-21 FIX (backend + frontend) bug #55
    [config.py, forms.py, models.py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]
2016-02-28 FIX (backend) missing setting on updated old systems dont get generated
    [settings.py, views.py]
2016-02-28 FIX (backend) missing argument for setting fix
    [settings.py]
2016-02-28 FIX (backend) fix converting bug
    [statistics.py]
2016-02-28 FIX (backend) conversion bug for incrementalSetOrUpdate
    [statistics.py]
2016-02-28 FIX (backend + frontend) stat-entry parsing
    [statistics.py]
2016-05-16 FIX (backend) problems to setup on windows
    [platform.py, settings.py]
2016-06-10 FIX (backend) problems while updating statistics after user god deleted.
    [worker.py]
2016-07-04 FIX (backend) bug in config-templates, reading out a list of string instead a single string
    [roseGuarden_Test_Withdraw.py, views.py, worker.py]
2016-08-11 FIX (backend) print caused error with utf8 chars
    Redirect the stdout-stream through a UTF8-writer
2016-10-14 IMPROVE (doc) add hint to bugfix spi-connection on rapsberry pi 2
2016-10-14 FIX (backend) the intepretation of the setting NODE_DOOR_AVAILABLE
    [views.py]
2016-10-16 FIX (backend) not working gpios for raspberry pi 2 boards
    [GPIO.py]
2016-10-17 FIX (backend) not working rfid for raspberry pi 2 boards
    [GPIO.py, RFID.py]
2016-11-05 FIX (backend) SPI-Py for correct SPI-settings and update RPi.GPIO
    [spi.c]
2016-11-05 ADD (hardware) new terminal construction
    [terminal1.FCStd]
2016-11-05 FIX (backend) buck while updating the profile
    [views.py]
2017-01-15 FIX (backend) wrong query for visible doors
    [views.py]
2017-02-10 ADD (hardware) add second version of terminal-case
    [terminal_v1.FCStd, terminal_v2_cap.FCStd]
2017-06-21 FIX (backend) naming issue with GPIOMockup (now named GPIOStub)
    [worker.py]

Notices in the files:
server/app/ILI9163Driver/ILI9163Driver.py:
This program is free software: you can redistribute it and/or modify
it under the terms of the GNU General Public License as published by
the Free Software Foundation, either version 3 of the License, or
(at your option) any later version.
